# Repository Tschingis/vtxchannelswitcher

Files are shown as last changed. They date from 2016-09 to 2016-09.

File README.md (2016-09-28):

# VTX Channel Switcher

This project is a nice little helper for people who are using video transmitters in quadrocopters or other remote controlled vehicles with a VTX. It allows to switch the video channel of a unify vtx with the attached remote control utilising a rc channel. It consists of a hardware part which connects the rc channel to the unify vtx and a lua script extension for the wide spread taranis remote control to setup the vtx channel.

## Features

* Switches VTX channel between race band 1 to 8
* Security feature to disallow channel change after a predefined timeout after powerup
* LUA Gui script for FrSky Taranis

## Restrictions

* Works currently only with unify vtx with smartaudio support (V1 or V2) (tested Unify 5.8 Pro HV)
* Might not work with connected microphone on audio pin, since a cheap voltage divider (5V to 3.3V) is used to interface the unify. (Maybe someone tests this). The board could be easily changed to run directly from a 3.3V power supply, when available, so no voltage divider is needed.
* LUA Script works only with OpenTX remotes (Taranis tested), but the vtx channel switcher can also be controlled with a poti on the remote control.

## Required Knowledge

If you want to build such a device yourself you should be familar with arduino ide and programming mcus utilising the ISP interface, although i will try to explain the most parts or link needed tutorials. In addition you should know how to solder mcus or in general electronics.

## Required Tools

In order to build a VTX channel switcher you need the following tools

* Solder iron
* Any arduino supported Atmel ISP Programmer (i.e. USBAsp or ArduinoISP)
* Required parts for the circuit (found in circuit, ATTiny13A MCU,some resistors and a capacitor)
* Multimeter with frequency measurement (not always needed)

## Building the Hardware

The interface between the rc receiver (or flight controller) and the unify vtx is a rather simple circuit which consist mainly of an ATTiny13A. This mcu is very low cost and needs nearly no additional parts to run reliable. The pcb is found in the circuit folder. You can use the provided pcb which uses SMD parts or you can just build your own version with DIP parts from the schematic. The required VCC is 5V.

## Building the MCU Software 

The software for the MCU is build with arduino since its easy to install and use. So install the following software

* [Arduino IDE 1.6](https://www.arduino.cc/)
* ATTiny13 Core for arduino 1.6 [Core13](https://sourceforge.net/projects/ard-core13/?source=navbar)  the version *core13_022_arduino_1_6.zip*. Installation is done by unzipping the downloaded file and then put the folder *attiny13* into *Your User/documents/Arduino/hardware*. If the directory should not exist, create it.

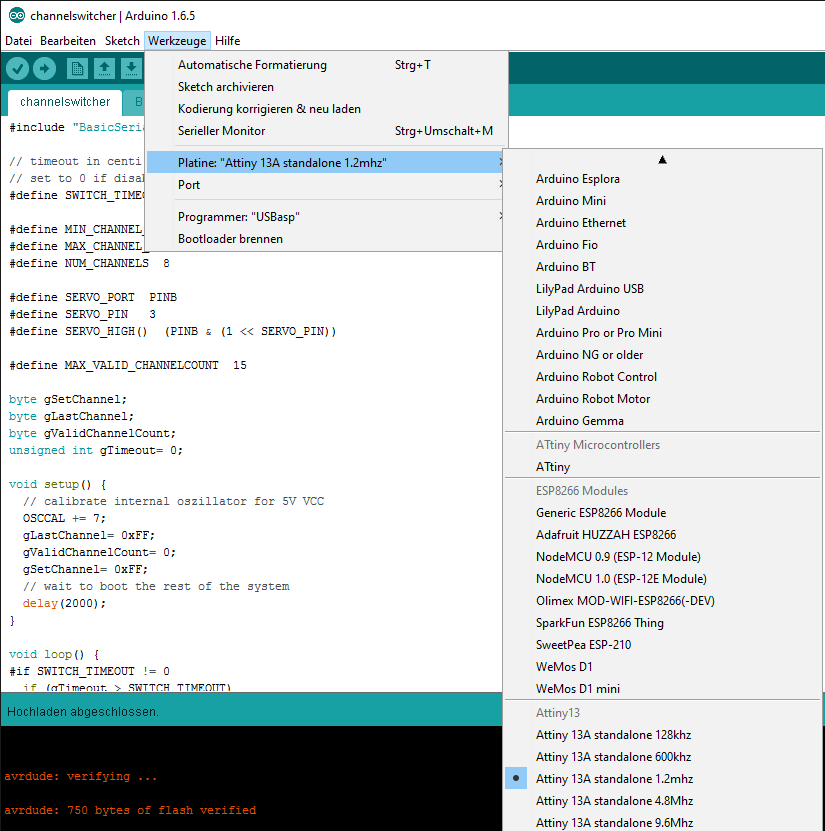
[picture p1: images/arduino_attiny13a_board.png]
Arduino Board Selection
After the installation of the Arduino IDE and the required ATTiny13 Core you should start the Arduino IDE and check if the ATTiny13 can be select as a board. 

If everything went ok, you should select the board *Attiny 13A standalone 1.2mhz*. Now open the arduino project which can be found in the channelswitcher directory. The sketch should compile ok when you press the verify button. You are now ready to flash the mcu.

## Flashing the ATTiny

Flashing a standalone attiny is not as comfortable as most arduino boards since you have to use the Atmel ISP interface of the mcu to flash it. In order to use the ISP you have to connect the ISP programmer to the attiny. The supplied pcb layout does not provide any solder points to connect the ISP lines to the attiny. You should just solder some cables directly to the mcu pins for programming (or if you are using a DIP part you could use a socket) which will be removed afterwards. I will not go into too much detail of how to connect the ISP to the attiny13 as there are many tutorials out there which show how to connect it. The attiny13 is pin compatible (in respect to ISP) with the attiny45/85 so you can also use a tutorial for these MCUs on how to wire up the MCU against the ISP. If you are using an ArduinoISP the wiring would be 

* Arduino +5V      --->  ATtiny Pin 8
* Arduino Ground --->  ATtiny Pin 4
* Arduino Pin 10   --->  ATtiny Pin 1
* Arduino Pin 11    --->  ATtiny Pin 5
* Arduino Pin 12    --->  ATtiny Pin 6
* Arduino Pin 13    --->  ATtiny Pin 7

When everything is connected and powered up you should be able to program the attiny by pressing the upload button in the arduino ide. If the programming fails, check the connections. Pin 1 on the attiny is marked with a small triangle on top. There should also be no connection between the isp connection wires (solder blobs etc.).

## Connecting the VTX Switcher to the Unify VTX

The connection to the unify vtx is rather simple since you have only to connect the audio cable from the unify with the smart audio pad of the vtx channel switcher.

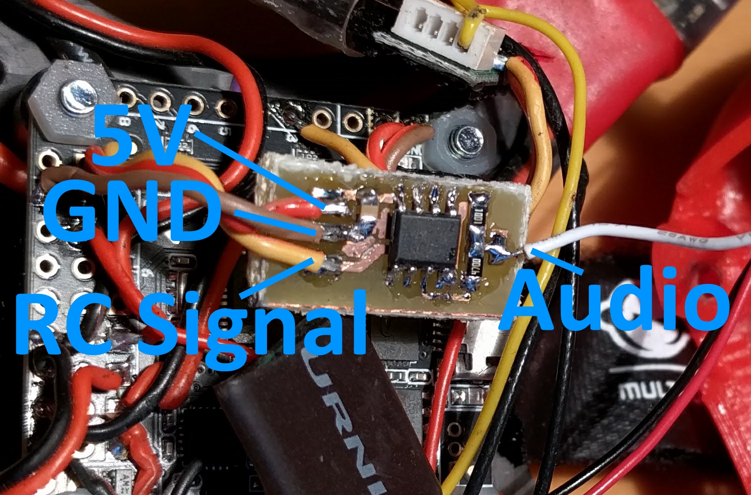
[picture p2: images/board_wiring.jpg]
Board Wiring


## Setting up the Flight Controller for Channel Forwarding

The most common use-case for this project will be, that it is installed inside a copter which is controlled by a flight controller. Nowadays the most users have serial receiver installed which will not output the required servo signal for the vtx channel switcher. I will show for some flight controllers how to setup a channel forwarding which puts the required servo signal on a pwm output of the flight controller

### Setting up Betaflight/Cleanflight

Betaflight/Cleanflight has the possiblity to output a servo signal to the pwm(esc) pins. I tested it only with a RMDO board but it should apply to other boards as well. Betaflight can enable channel forwarding in the feature section of the configurator but this just leads to frustration as it does not activate all required features so just open the CLI and type

    feature CHANNEL_FORWARDING 
    feature SERVO_TILT
    save

Now you can setup a servo mapping in the configurator gui. On most F3 targets ESC pins 7-8 map to servo 0-1. The servo pane actually maps an input channel to a servo(ESC pin). Just set a checkbox on the input which should be used for the servo, i.e. check the box *A2* on *Servo 0*. Now you have mapped Aux2 input channel to ESC Pin 7 (servo0), the rest of the servo settings should be kept untouched.
Servo Mapping

### Setting up KISS FC

For the KISS FC its much easier (as supposed). In the AUX1-4 channel section you should just select one of the functions *PWM5: Servo Mid* or *PWM6: Servo Mid*. This maps the input from the selected AUX channel to the PWM5 or PWM6 output pin of the KISS FC.

## Setting up Taranis Channel Switcher LUA Script

The FrSky Taranis is a very nice radio with excellent software support. This allows us to put a LUA script on the Taranis (SD Card) and show a custom screen which modifies the model memory in order to send the correct servo signal for a specific video channel. 
The script actually computes a global variable value for GV1 (can be changed to any other if already used) which is then used inside a mixer to generate an usuable servo signal for the vtx channel switcher. 
The first step is to copy over the *channelselector.lua* script from the repository *opentx* directory to the sd card of the taranis. You can put it anythere on the sd card, but you should use the root of the card since there will be no shortcut (switch assignment) to the script and you have to navigate to the script in the sd card browser of the taranis. 
The next step is to create a new mixer for the rc channel which has been mapped previously to the vtx channel switcher hw. Open the mixer settings and change the following values

    Source -> MAX
    Weight -> GV1  (long enter press on the weight allows to assign global variables)
    
## Starting the LUA Script

You can now start the *channelselector.lua* script when you are on the main screen of the taranis by a long press on the menu button and then go to the sd card browser (page btn). In the sd card browser navigate to the script and execute it (select it with enter and choose *Execute*). **Have Fun**

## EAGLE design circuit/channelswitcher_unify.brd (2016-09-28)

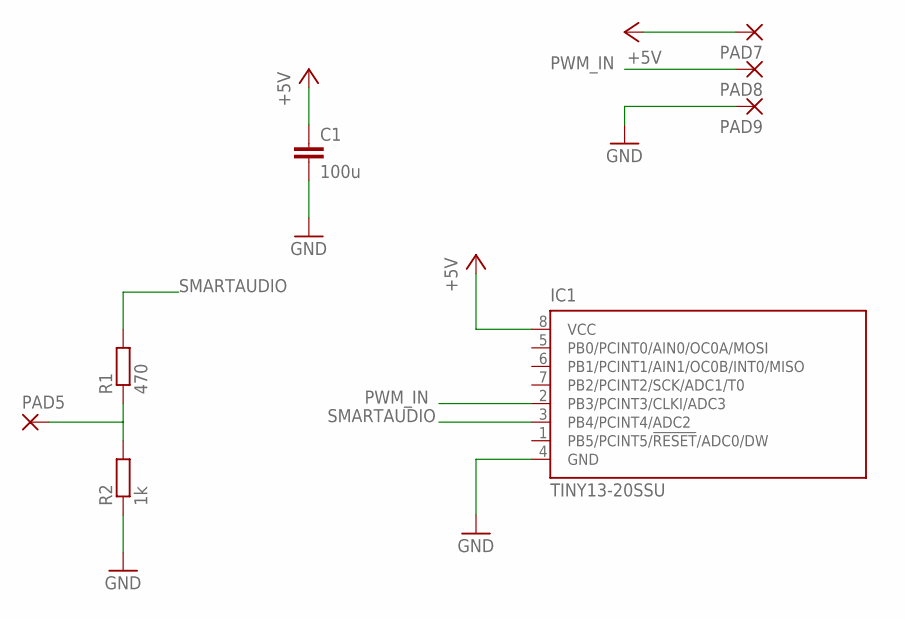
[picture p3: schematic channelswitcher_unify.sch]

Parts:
C1: 100u; C0805
IC1: TINY13-20SSU; 8S1
PAD5, PAD7, PAD8, PAD9: SMD2; SMD1,27-2,54
R1: 470; R0805
R2: 1k; R0805

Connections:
+5V: C1.1, IC1.8 (VCC), PAD7.1
GND: C1.2, IC1.4 (GND), PAD9.1, R2.1
unnamed: PAD5.1, R1.1, R2.2
PWM_IN: IC1.2 (PB3/PCINT3/CLKI/ADC3), PAD8.1
SMARTAUDIO: IC1.3 (PB4/PCINT4/ADC2), R1.2

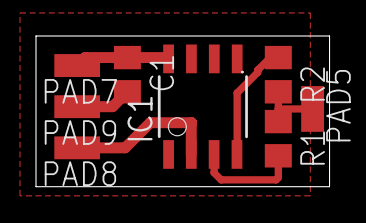
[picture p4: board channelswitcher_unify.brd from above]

Board: 2 copper layers, 16.3 x 8.4 mm, 8 parts (0 on the bottom side), 5 nets.

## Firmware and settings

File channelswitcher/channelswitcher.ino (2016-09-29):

/*
VTX Channel Switcher
Author: Markus Wilhelm
*/

#include "BasicSerial3.h"

// timeout in centi seconds after which servo signal will no longer evaluated and a restart is required
// set to 0 if disabled
#define SWITCH_TIMEOUT  300

#define MIN_CHANNEL_CMD 1000
#define MAX_CHANNEL_CMD 2000
#define NUM_CHANNELS  8

#define SERVO_PORT  PINB
#define SERVO_PIN   3
#define SERVO_HIGH()  (PINB & (1 << SERVO_PIN))

#define MAX_VALID_CHANNELCOUNT  15

byte gSetChannel;
byte gLastChannel;
byte gValidChannelCount;
unsigned int gTimeout= 0;

void setup() {
  // calibrate internal oszillator for 5V VCC
  OSCCAL += 7; 
  gLastChannel= 0xFF;
  gValidChannelCount= 0;
  gSetChannel= 0xFF;
  // wait to boot the rest of the system
  delay(2000);
}

void loop() {
#if SWITCH_TIMEOUT != 0
  if (gTimeout > SWITCH_TIMEOUT)
    return;
  ++gTimeout;
#endif

  evalChannel();
  delay(100);
}

void evalChannel()
{
  byte channel= readChannel();
  if (channel >= NUM_CHANNELS) {
    gValidChannelCount= 0;
    return;
  }

  if (channel != gLastChannel) {
    gLastChannel= channel;
    gValidChannelCount= 0;
    return;
  }
  ++gValidChannelCount;
  if (gValidChannelCount < MAX_VALID_CHANNELCOUNT)
    return;
  gValidChannelCount= 0;

  if (channel != gSetChannel) {
    transmitChannel(channel);
    gSetChannel= channel;
  }
}

byte readChannel()
{
  unsigned int pulse= readServoPulse();
  // put into range
  if (pulse < MIN_CHANNEL_CMD)
    return 0xFF;
  if (pulse > MAX_CHANNEL_CMD)
    return 0xFF;

  unsigned int pos= pulse - MIN_CHANNEL_CMD;
  return pos / ((MAX_CHANNEL_CMD - MIN_CHANNEL_CMD) / NUM_CHANNELS);
}

// external overflow variable from attiny13 arduino core
extern unsigned long ovrf;
unsigned int readServoPulse()
{
  // turn off timer0 and reset all state variables
  TCCR0B= 0;  
  TCNT0= 0;
  ovrf= 0;
  
  // wait until low
  while(SERVO_HIGH()) {}

  // wait until high (signal start)
  while(!SERVO_HIGH()) {}

  // enable timer0 with system clock
  TCCR0B= (1 << CS00);  
  while(SERVO_HIGH()) {}
  TCCR0B= 0;

  if (ovrf > 0xFF)
    return 0xFFFF;
    
  // make one big timer value and convert tick to uS (divide by 1.2)
  return ((((unsigned int)ovrf << 8) | TCNT0) * 5) / 6;
}

void transmitChannel(byte channel)
{
  if (channel > 8)
    return;
    
  // precomputed crc8
  // 0: 0x1C
  // 1: 0xC9
  // 2: 0x63
  // 3: 0xB6
  // 4: 0xE2
  // 5: 0x37
  // 6: 0x9D
  // 7: 0x48
  const byte preCompCrc8[8]= { 0x1C, 0xC9, 0x63, 0xB6, 0xE2, 0x37, 0x9D, 0x48 };
  
  byte cmd[6];
  cmd[0]= 0xAA;
  cmd[1]= 0x55;
  cmd[2]= 0x07;
  cmd[3]= 0x01;
  cmd[4]= 32 + channel;  // Race Band offset 32
  cmd[5]= preCompCrc8[channel];

  TxByte((byte)0);

  for(int i= 0; i < 6; ++i) {
    TxByte(cmd[i]);
  }

  TxByte((byte)0);
  // set tx pin to input
  UART_DDR &= ~(1<<UART_Tx);
}

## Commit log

2016-09-28 Add image of attiny13 board selection
2016-09-28 -added channel switcher arduino sketch
2016-09-28 -added image for board wiring
2016-09-28 -added servo mapping from bf configurator
2016-09-28 -added circuit and lua script
    [channelswitcher_unify.brd, channelswitcher_unify.sch]
